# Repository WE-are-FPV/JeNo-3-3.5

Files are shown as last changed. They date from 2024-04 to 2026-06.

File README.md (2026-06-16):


> [!NOTE]
> Current version : **1.2.1** (read [changelog](#changelog) for details)

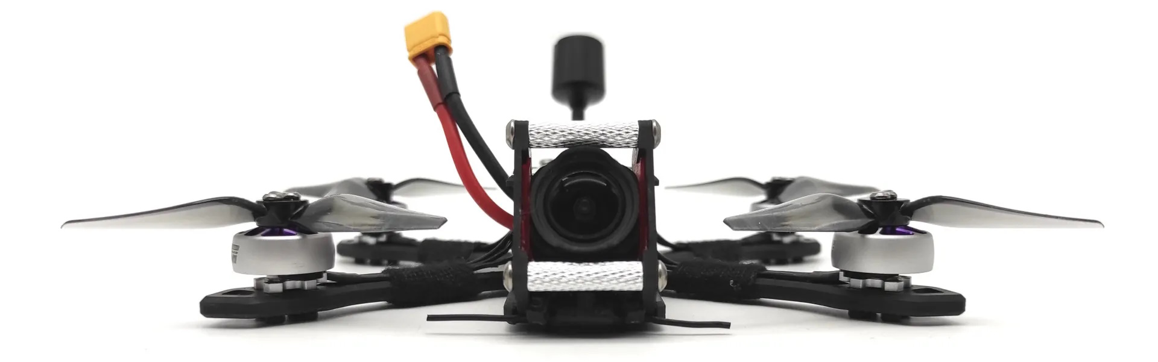
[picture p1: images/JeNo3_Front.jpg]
JeNo 3 - Front view


# JeNo 3" and 3.5"
***3-3.5" drone FPV frame compatible with Air Unit O3 and O4 Pro, designed for Freestyle, Freeride and Cinematic. Many customizable options are available.***

> [!NOTE]
> Designed in France by members of the [WE are FPV](https://www.wearefpv.fr/) community, the JeNo is already flown by hundreds of pilots and is now being sold by [Drone FPV Racer](https://www.drone-fpv-racer.com/jeno-3-frame-kit-we-are-fpv-12958.html?aff=64&id_campaign=13) (affiliate link). The French version of the project is available on [Printables](https://www.printables.com/fr/model/459702-jeno-335-drone-frame). Note that a [2.5" version](https://github.com/WE-are-FPV/JeNo-Pocket), a [5.1-6" version](https://github.com/WE-are-FPV/JeNo-5.1) and a [7-8" version](https://github.com/WE-are-FPV/JeNo-7) of the JeNo exist.

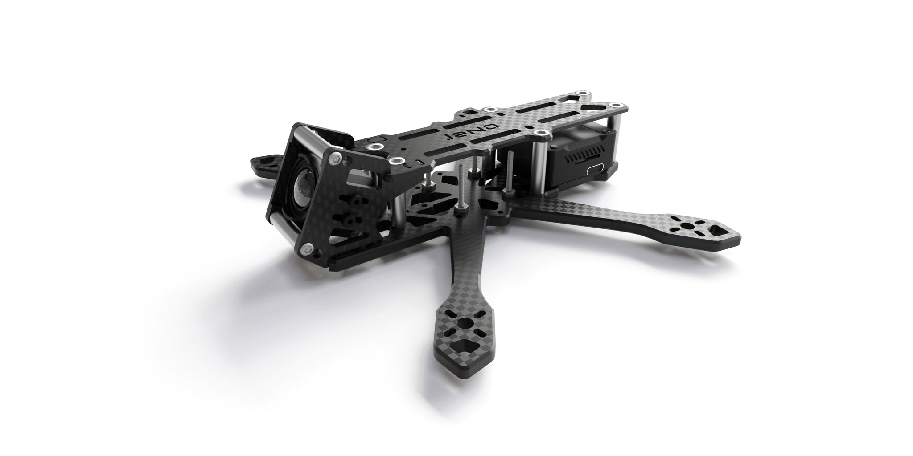
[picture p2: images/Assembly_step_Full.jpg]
JeNo classic - 3D render


## Table of contents

* [Key features](#key-features)
* [Presentation](#presentation)
* [Detailed specifications](#detailed-specifications)
* [Versions and files](#versions-and-files)
* [Customization](#customization)
* [Buy it or cut it !](#buy-it-or-cut-it-)
* [Bill of materials](#bill-of-materials)
* [Building/Assembly guide](#buildingassembly-guide)
* [Inspiration](#inspiration)
* [Tuning, Betaflight Preset ?](#tuning-betaflight-preset-)
* [Blackbox](#blackbox)
* [Videos](#videos)
* [Builds examples](#builds-examples)
* [Authors](#authors)
* [TPU](#tpu)
* [Community (remixes and TPU)](#community-remixes-and-tpu)
* [Changelog](#changelog)

## Key features
- [x] **Sturdiness** and **rigidity**
- [x] Excellent flight **performances**, easy to tune
- [x] **Wide-X** geometry
- [x] Perfect DJI **Air Unit O3 or O4 Pro** camera integration
- [x] Optional soft mounting of the camera for effective Gyroflow stabilization.
- [x] Designed for : DJI Vista/AU O3/AU O4 Pro, WalkSnail, HDZero, Analogic
- [x] **Frame and standoffs NOT visible** in video feed, with any FPV camera
- [x] **Props NOT visible** in video feed !
- [x] Support 20x20 stacks as well as AiO (straight and 45° angled)
- [x] **Customizable** (weight, size, camera plates, unibody or not)

## Presentation
The success of the [JeNo 5.1"](https://github.com/WE-are-FPV/JeNo-5.1) has led us to develop a little brother, in **3 and 3.5"** form factor. This frame will therefore be just **as comfortable for Freestyle as for cinematic** shooting.

On 5" and larger builds, we might be tempted to keep an Action Cam, whereas on a **compact and light machine**, the **DJI O3/O4 Pro reveals its full potential**.

The design of a frame of this size turned out to be more delicate than expected :

* **Weight** is crucial
* **Strength** and **rigidity** remain major concerns
* **Electronics** are more **diversified** : 20x20 stack with separate FC and ESCs, AiO straight or angled at 45°, stack mounting with M2 or M3...
* The low inertia of this format makes the gyro of the O3/O4 Pro camera very sensitive; vibration tolerance is much lower than for a 5" quads
* **Clear FOV** : no spacers, frame, or visible propellers in the FPV feed

After several iterations, we have come to a first version of the JeNo that **ticks all these boxes !** This is the **3" Classic version, unibody with a 4mm bottom plate**.

We were initially not enthusiastic about the unibody design, but this approach has proven to be an **excellent compromise**. With a thickness of 4mm for the bottom plate, we get **exceptional strength** and **flight behavior** worthy of a 5". The assembly remains easy, and the absence of separate arms allows for sliding a 20x20 stack while taking advantage of the 20mm height of the body.

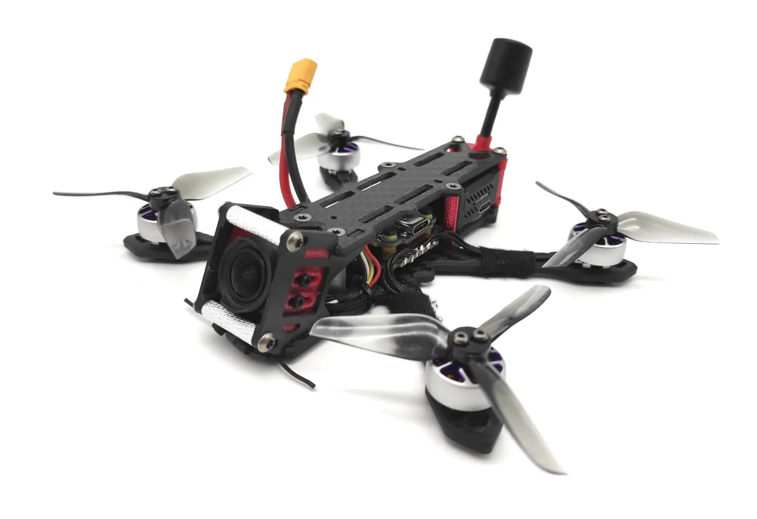
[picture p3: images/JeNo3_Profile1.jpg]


**Other versions** are available :

* 3.5" (unibody) (warning : tips of props slightly visible in the FPV feed)
* 3" (unibody) **Light**
* 3" et 3.5 " with **separate arms**
* 4": this is a variation created by Kennytak, and the necessary files are available on [his page](https://www.printables.com/fr/model/516544-jeno-4-unibody-drone-frame-for-dji03-airunit-vista). The props remain slightly visible in the FPV feed.

The **JeNo 3** follows in the footsteps of its big brother : the front cage tilted at 25° provides a **clear FOV**. Notches are provided to slide in any type of **ND filter**, and the propellers are not visible in the FPV feed or in HD recording.

Be cautious, though—when using an O4 Pro, make sure to get vertical ND filters, like [those from GEPRC](https://geprc.com/product/geprc-dji-o4-air-unit-pro-filter/).

Two types of camera plates are available : **full carbon** or **soft-mounted**. Note that to benefit from Gyroflow (or RockSteady) stabilization, it is **imperative to opt for the soft-mounted camera plates**.

Finally, as this frame was designed by members of the [WE are FPV](https://www.wearefpv.fr/) **community**, a **"WaF edition"** is available (the logo is engraved on the bottom plate). Join us on the WAF forum in [the official JeNo 3-3.5" thread](https://forum.wearefpv.fr/topic/20437-jeno-335-un-ch%C3%A2ssis-compact-taill%C3%A9-pour-le-dji-o3/) to discuss it further.

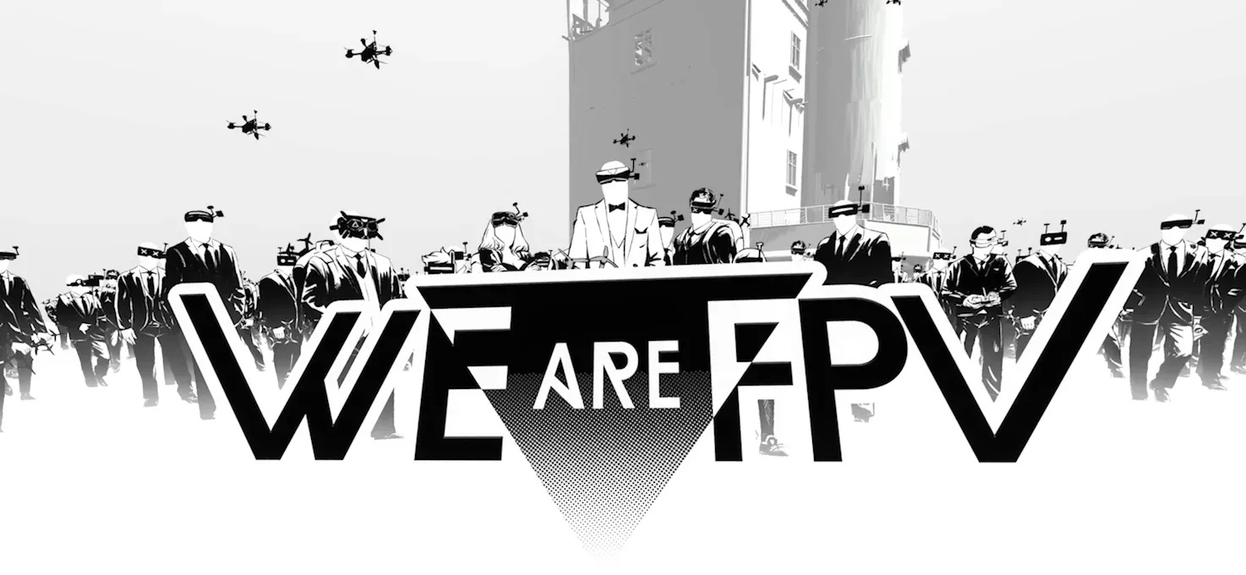
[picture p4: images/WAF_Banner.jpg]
WE are FPV banner


The JeNo is also available in [2.5" version](https://github.com/WE-are-FPV/JeNo-Pocket), [5.1" and 6" version](https://github.com/WE-are-FPV/JeNo-5.1) and [7" and 8" version](https://github.com/WE-are-FPV/JeNo-7).

## Detailed specifications

||| 
| :--- | :--- |
| **Geometry** | **Wide-X** | 
| **Props size** | 3 to 3.5" (depending on the versions) | 
| **Weight** | **40 to 55 g** depending on the versions, including screws | 
| **Arms** | **4mm** for unibody, **3mm** for separate arms | 
| **Body height** | 20 mm | 
| **Stack height** | 20 mm (unibody) | 
| **Bottom plate** | **4mm** for unibody, **2mm** for separate arms | 
| **Middle plate** | 2 mm (separate arms) | 
| **Top plate** | 2 mm | 
| **Camera plates** | 2.5 mm | 
| **Motors mounting** | 9 to 12 mm | 
| **Camera** | 20 mm (DJI), Micro, Nano. **Clear FOV**. Ajustable.
| **Main stack** | 25.5 mm x 25.5 mm (M2) AiO and 20 mm x 20 mm (M2) stack | 
| **Supported VTX** | Analogic, DJI Vista, **DJI Air Unit O3/O4 Pro**, WalkSnail, HDZero… | 
| **Strap passage** | Yes | 

## Versions and files

### Versioning
You will find the **current version** of the frame at the beginning of the description and the full [history of modifications](#changelog) at the end of the page.

We strongly recommend always cutting the latest version to ensure you benefit from the most recent optimizations.

The version **number format** is as follows :
```
<Major versions>.<Minor version>.<Revision>
ex : 1.3.2
```

* **Revision :** This number is incremented in the case of minor modifications with no significant impact.
* **Minor version :** This number is incremented for minor modifications that may potentially break compatibility with certain TPU parts.
* **Major version :** This number is incremented for significant modifications that break compatibility at the carbon level.

Since the creation of the JeNo 3", we have always strived to **maintain compatibility at the carbon level**. As a result, the version remains “1.x.y.”

In practical terms, this means that if you have the very first version of the JeNo 3" and want to equip it with the **O4 Pro**, you only need to have new camera plates cut—they will be compatible with your frame version!

**Note :** If you develop TPU parts for the JeNo, be sure to specify the version they are compatible with.

### Files management
To simplify things, we have reorganized the file structure. The files are now divided into **five groups** :

* **01-FRAME :** Contains **models** describing the **frame** in DXF, STEP, and STL formats for the current version. Also contains a PDF file which is a reformatted version of the DXF.
* **02-TPU :** Contains **TPU models** for the current frame version in STL format.
* **03-FRAME-HISTORY :** Contains previous versions of the frame.
* **04-TPU-HISTORY :** Contains TPU models that are no longer compatible with the current version.
* **OTHER-FILES :** Contains documentation files, including the assembly manual and a description.

The major change is that all options are now consolidated into a single file. This will make version management significantly easier for us.

If you want to view the DXF file with all annotations, we recommend using the free software [DWG TrueView](https://www.autodesk.com/products/dwg-trueview/overview). If you prefer not to use it, the PDF version of the file will contain all the necessary information.

## Customization

The JeNo is customizable, offering several **options** to best adapt to different needs and individual preferences : 

* **3" Unibody 4mm Classic :** This is the first version made available. Designed for **freestyle** due to its strength, it will also be suitable for **cinematic** use with soft-mounted camera plates. 100% clear FOV. This version uses **M3** screws and standoffs.
* **3" Unibody 4mm Light :** Sacrificing some strength and rigidity for more lightweight, thus increasing autonomy, and switching to **M2** screws/spacers. A chassis more oriented towards cinematic use. Note that M2 standoffs are more difficult to source.
* **3.5" Unibody 4mm :** For those seeking a bit more **inertia and stability**, or possibly for mid-range use. _**Note: the propellers are very slightly visible in the FPV feed. With black propellers, they will be practically invisible.**_
* **Separate arms :** For those wary of unibody designs ;) a 3" version and a 3.5" version (only the length of the arms changes). _**Note: AIO strongly recommended; stacks will struggle to fit due to the low remaining height in the body = low profile !**_

Several versions of 25° camera plates are available :

* **Freestyle** (full carbon): Optimized for the O3.
* **Cinematic** (soft-mounted): Optimized for the O3.
* **M2 versions** for the Light edition.
* **Freestyle O4 Pro** (full carbon): Optimized for the O4 and compatible with the O3.
* **Cinematic O4 Pro** (soft-mounted): Optimized for the O4 and compatible with the O3.

A [high tilt version](https://www.thingiverse.com/thing:6584519) (40°) is available in community remixes (by [Bard Fpv](https://www.youtube.com/@bardfpv)) for the O3.

> [!IMPORTANT]
> Please note that to benefit from Gyroflow (or RockSteady) stabilization, **soft mounting is mandatory**.

> [!IMPORTANT]
By default, we have left the stack holes at a 2mm diameter (M2). If your stack uses M3 screws, you will need to enlarge these holes. Please note, carbon dust is hazardous, to avoid inhaling it, run a trickle of water while drilling/filing.

For your information, we have tested this frame with the following setup:

* **Recommended Motors :** 1404, 4000 to 4500KV for 3"
* **Recommended Batteries :** 4S / 550mAh for Freestyle, up to 850mAh for cinematic cruising
* **Recommended Props :** T3x2.5x3 & HQ T3x3x3

Below, you will find a complete build example as well as several flight videos with this setup.

## Buy it or cut it !

It is up to you : you can get it cut or you can get it from a shop. If you're not looking for a specific option, note that Drone FPV Racer offers the JeNo 3" in the classic version, along with all spare parts, prints, and lipo pads. La Camera Embarquée also offers the JeNo 3 and 3.5".

* [JeNo 3" by DFR](https://www.drone-fpv-racer.com/jeno-3-frame-kit-we-are-fpv-12958.html?aff=64&id_campaign=13) (affiliate link)
* [JeNo 3" by DFR](https://www.lacameraembarquee.fr/we-are-fpv/17773-chassis-we-are-fpv-jeno-3.html)
* [JeNo 3.5" by DFR](https://www.lacameraembarquee.fr/we-are-fpv/17776-chassis-we-are-fpv-jeno-35.html)
* [FPV CNC Drone](https://fpvcncdrone.com/)

The JeNo 3" and all its variations are also available from [CNC Madness](https://cncdrones.com/WE-are-FPV_c_118.html) (Canada).

Of course, you can directly contact your favourite carbon fiber cutting service.

Note: Prices are often excellent in stores, but they don’t always offer the latest version.

The ["01-FRAME"](https://github.com/WE-are-FPV/JeNo-3-3.5/tree/main/01-FRAME) folder contains all the files you need to get it **cut** in your favourite flavour.

Consult the **DXF file** of the frame (or the PDF version) to choose the version that interests you.

Feel free to select a pre-made "Edition" (Classic, Light, or Bando), or mix different options and choose certain "extras".

You will also need to choose a type of camera plates (classic, cine, etc.).

> [!NOTE]
> All parts versions are compatible with each others

## Bill of materials

In addition to the carbon fiber, you will need the following hardware to complete the assembly of the frame.

**Standoffs**

It is recommended to use 5mm diameter standoffs, especially for those that will serve as support for TPU (backpack and capacitor). Moletted standoffs can still be used, but the TPU supports will need to be modified accordingly.

> [!WARNING]
> Attention: For the Light version, you will need to provide M2 standoffs and corresponding screws (M2 instead of M3)

| Quantity | Description | Details |
| :---: | :--- | :--- |
| 6 | M3x20mm standoffs | for the body |
| 2 | M3x20mm standoffs | for the camera |

**Stack materials**

> [!WARNING]
> Attention: M2 screws are mentioned here because they are most commonly found in this format. However, some 20x20 stacks use M3 screws. In this case, you will need to enlarge the stack holes.

* If 25.5x25.5 AiO

| Quantity | Description | Details |
| :---: | :--- | :--- |
| 4 | M2x16mm | for the stack |
| 4 | M2 nuts for stack screws | |

* If 20x20 stack

| Quantity | Description | Details |
| :---: | :--- | :--- |
| 4 | M2x20mm countersunk screws | for the stack |
| 4 | M2 nuts for stack screws | |

**Frame materials**

| Quantity | Description | Details |
| :---: | :--- | :--- |
| 6 | M3x6/8mm countersunk screws | for the top plate |
| 10 | M3x8mm screws (titanium if possible) | for the bottom and camera plates |

**Additional materials**

| Quantity | Description | Details |
| :---: | :--- | :--- |
| 16 | M2x7mm screws (if using arms protections) or M2x6mm (if no TPU) | for the motors |
| 4 | M2x3mm screws if soft mounted or M2x4mm if NOT softmounted | for the camera |

**Additional materials for separate arms versions**

| Quantity | Description | Details |
| :---: | :--- | :--- |
| 5 | Pressnuts ([Flywoo](https://www.drone-fpv-racer.com/flywoo-m3-clinch-nuts-20-pcs-7965.html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) or SourceOne alike) | 4 for the arms, 1 for the middle plate |
| 5 | M3x10mm screws | for the pressnuts |

**Fasten the lipos**

The JeNo allows the use of non-slip straps thanks to its strap slots. You can also use a LiPo pad if desired.

## Building/Assembly guide

Find numerous examples of builds on the _**DroneBuilds**_ page of WE are FPV.
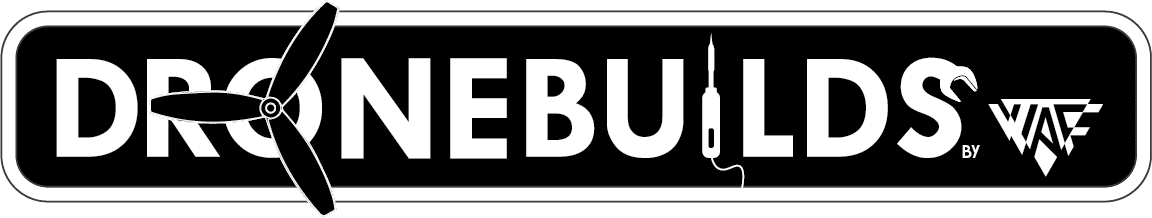
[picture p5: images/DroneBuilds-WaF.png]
DroneBuilds (https://forum.wearefpv.fr/71-dronebuilds/ "DroneBuilds - Click to Access!")


Some **clarifications** before assembling the frame:

* If your electronics require M3 screws, you will need to slightly enlarge the holes, originally designed for M2 (taking care not to inhale carbon dust)
* You can use the front standoffs to attach a capacitor and/or an RX :

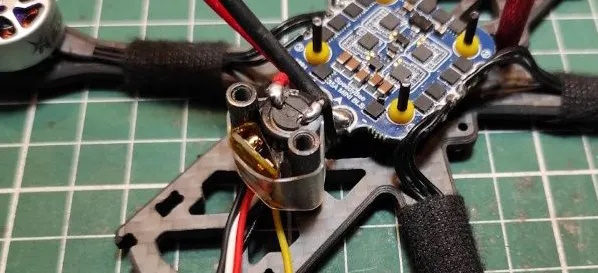
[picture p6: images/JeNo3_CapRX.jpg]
JeNo 3 Capacitor and RX


* The RX antenna can be attached to the front of the quad using zip ties (TPU front bumper also allow to fix the RX antenna)

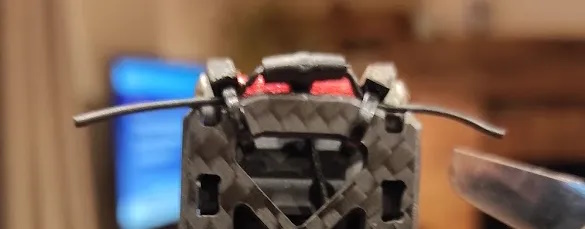
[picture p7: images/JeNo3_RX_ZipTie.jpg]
JeNo 3 RX Antenna


The assembly is simple (you can also find the detailed [assembly instructions in PDF format](https://github.com/WE-are-FPV/JeNo-3-3.5/blob/main/OTHER-FILES/JeNo3_Assembly_Guide_EN.pdf) among the project files) :

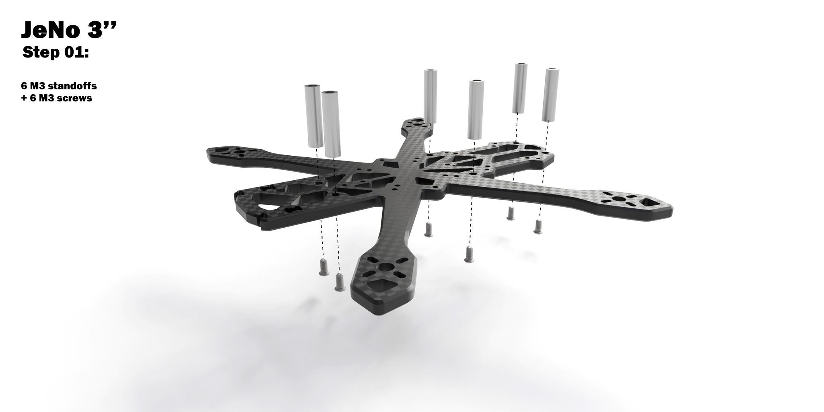
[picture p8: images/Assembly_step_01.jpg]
JeNo 3 Assembly step 01


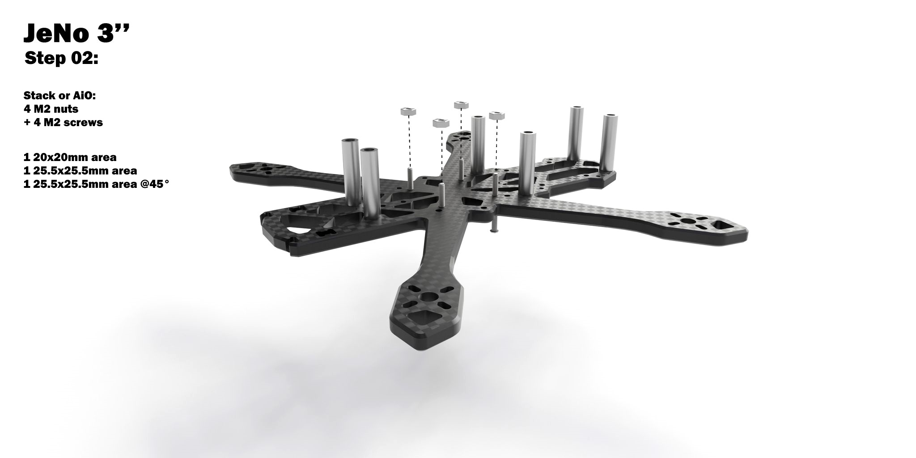
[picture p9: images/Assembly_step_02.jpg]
JeNo 3 Assembly step 02


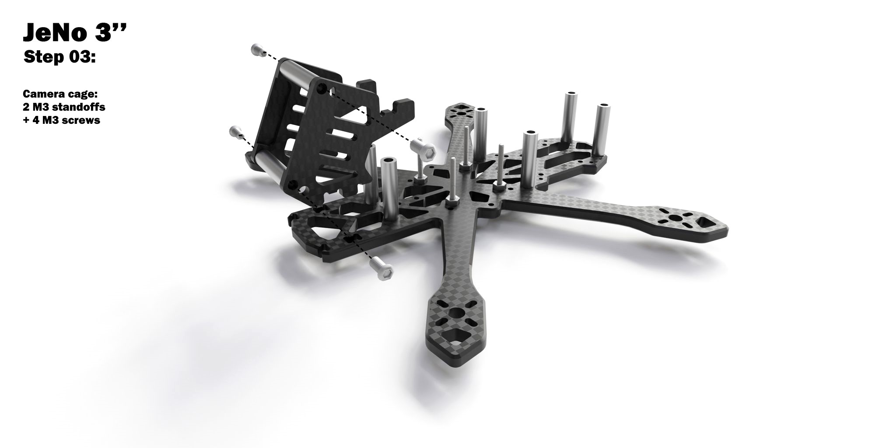
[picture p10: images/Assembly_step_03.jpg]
JeNo 3 Assembly step 03


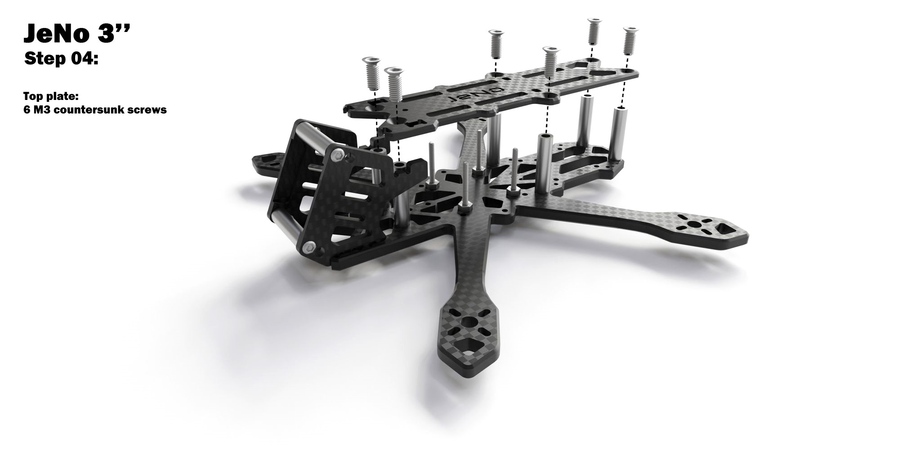
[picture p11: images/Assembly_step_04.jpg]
JeNo 3 Assembly step 04


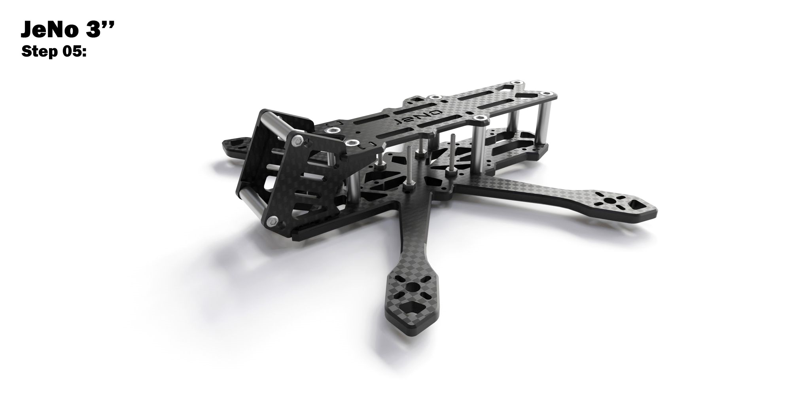
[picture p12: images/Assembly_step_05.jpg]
JeNo 3 Assembly step 05


## Inspiration
It is primarily inspired by its big brother, the [JeNo 5.1"](https://github.com/WE-are-FPV/JeNo-5.1), especially for the camera plates system.

## Tuning, Betaflight Preset ?
For the JeNo 5.1", we provided a preset.

For the 3", we will not share a preset in the short term because there are **too many factors** that can alter the quad's behavior:

* Bottom plate thickness
* Stack VS AiO (the latter often being much noisier)
* M3 screws and spacers vs M2
* 3" props vs 3.5"
* Capacitor or not
* etc.

If, with a little more perspective, we see that a preset is feasible, we will share it. In the meantime, we have shared some settings that should work with most setups in [this post](https://forum.wearefpv.fr/topic/20437-jeno-335-un-ch%C3%A2ssis-compact-taill%C3%A9-pour-le-dji-o3/page/10/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).

However, one piece of advice, if you find your quad too challenging to handle in confined spaces, do not hesitate to adjust the throttle curve by adding a bit of expo around the "hover point" :

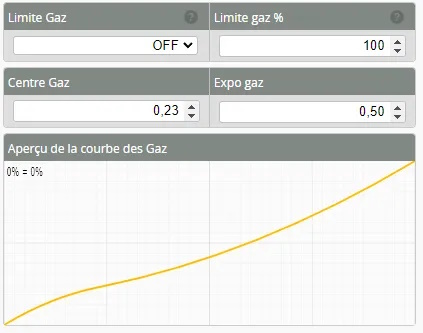
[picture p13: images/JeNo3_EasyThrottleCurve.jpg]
JeNo 3 Throttle curve


## Blackbox
Here is an overview of vibration distribution on the 3 axes for the JeNo 3" 4mm Unibody. This is indeed the **unfiltered** gyro signal freestyle flight :

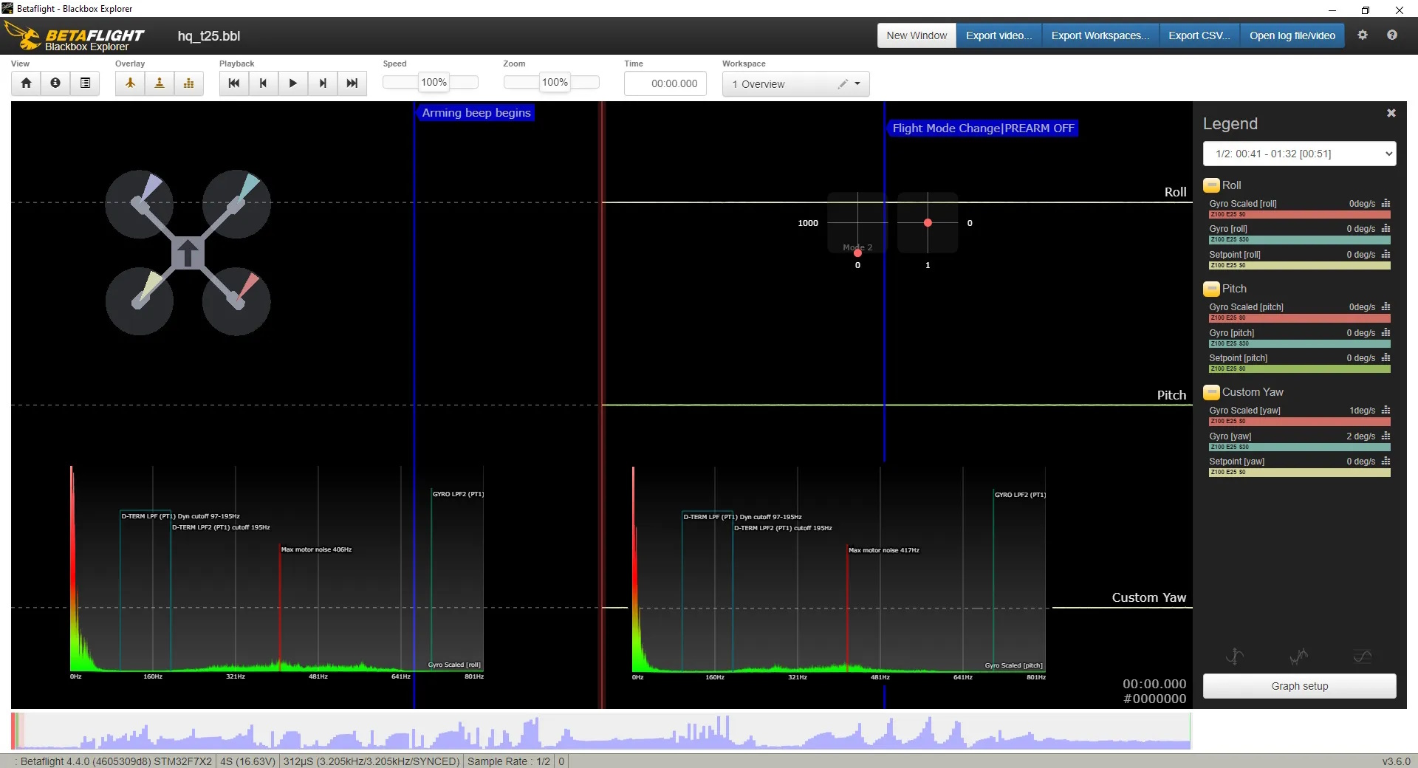
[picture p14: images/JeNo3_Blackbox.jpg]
JeNo 3 Blackbox


## Videos
Flight preview of the JeNo 3" Unibody Classic 4mm version (Cinematic, camera plates soft-mounted), stabilized with Gyroflow :

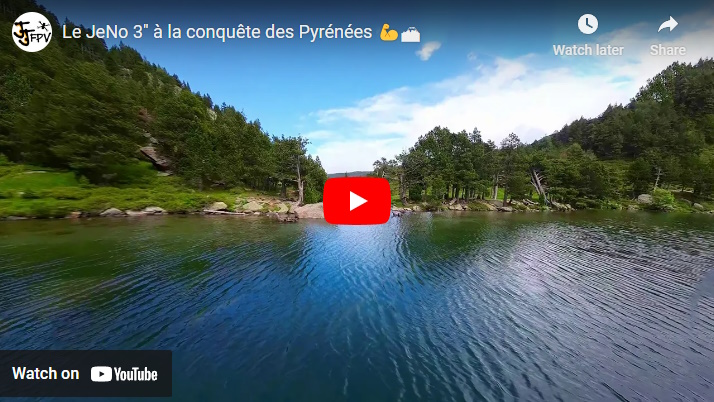
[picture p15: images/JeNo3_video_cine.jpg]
JeNo 3" Cinematic (https://www.youtube.com/watch?v=Bba9C5jj3qI "JeNo 3 Cinematic - Click to Watch!")


Flight preview of the JeNo 3" Unibody Classic 4mm version (Freestyle) :

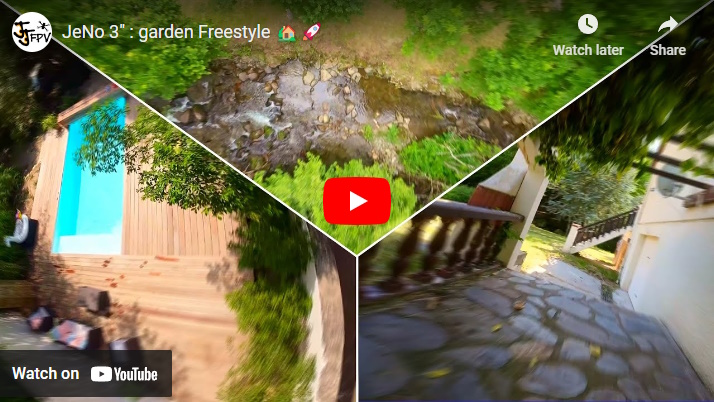
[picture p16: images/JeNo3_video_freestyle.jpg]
JeNo 3" Freestyle (https://www.youtube.com/watch?v=a-RcqAQSSa8 "JeNo 3 Freestyle - Click to Watch!")


Flight preview of the JeNo 3" Unibody Classic 4mm version (Bando):

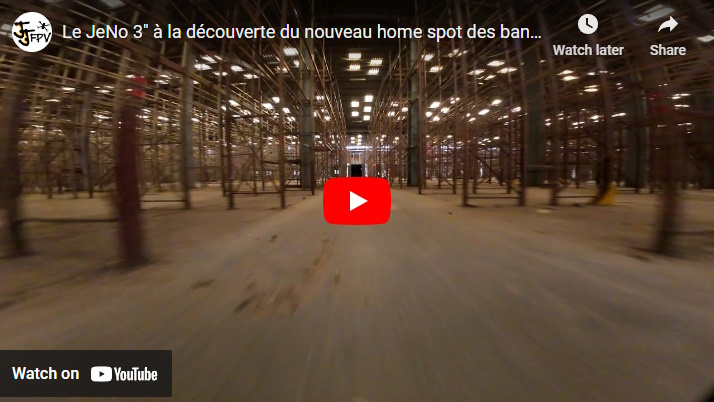
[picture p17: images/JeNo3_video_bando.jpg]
JeNo 3" Bando (https://www.youtube.com/watch?v=Iw_Cw9_1gNU "JeNo 3 Bando - Click to Watch!")


JeNo 3" review on WE are FPV (French) :

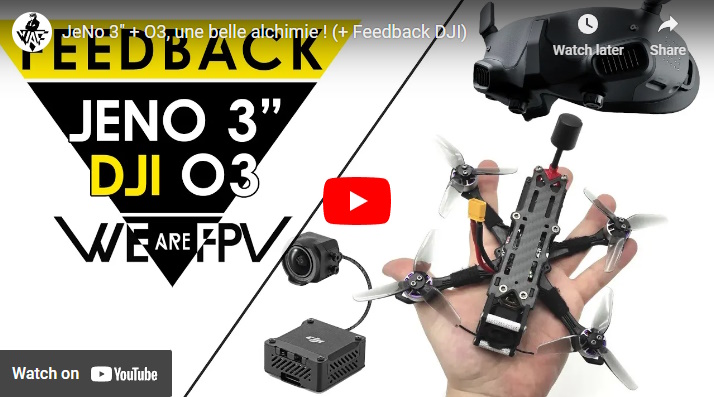
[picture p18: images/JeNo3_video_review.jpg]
JeNo 3" Review (https://www.youtube.com/watch?v=-c4rGYWvYhU "JeNo 3 Review - Click to Watch!")


## Builds examples

You can find many build examples on [WE are FPV's DroneBuilds](https://forum.wearefpv.fr/71-dronebuilds/) :

* fr : [JeNo 3 Prototype](https://forum.wearefpv.fr/topic/20327-proto-jeno-3/) (this one)
* fr : [JeNo 3" AiO AT32/AM32](https://forum.wearefpv.fr/topic/21637-jeno-3-aio-at32am32/)
* fr : [JeNo 3.5" O3](https://forum.wearefpv.fr/topic/20480-jeno-35_o3/)
* fr : [JeNo 3" (6s)](https://forum.wearefpv.fr/topic/22032-jeno-3-mais-en-6s-et-sous-testost%C3%A9rone/)
* fr : [Jeno 3" (Kiss)](https://forum.wearefpv.fr/topic/21647-jeno-3-kiss/)
* fr : [jeno3 light](https://forum.wearefpv.fr/topic/22677-jeno3-light/)
* ...

## Authors

The JeNo was designed by :

* nochamo - [Youtube](https://www.youtube.com/user/nochamo)
* Jerome / Jéjé FPV - [Youtube](https://www.youtube.com/@jejefpv)

## TPU
Among the [downloadable files](https://github.com/WE-are-FPV/JeNo-3-3.5/tree/main/tpu), you will find a variety of TPU to protect your JeNo 3" :

* **VTX Antenna** mounts
* Front and back **bumpers**
* **Nano camera** adapter
* Camera **softmount**
* Several arms **protections**

## Community (remixes and TPU)

**Fork/remix**

* [JeNo 4"](https://www.printables.com/fr/model/516544-jeno-4-freestyleracing-drone-frame-for-dji03-airun) by [Kennytak](https://www.printables.com/fr/@Kennytak_77000)

**TPU**

In addition to the TPU options available on [this repo](https://github.com/WE-are-FPV/JeNo-3-3.5/tree/main/tpu), you will find here some TPU designs created by the community.

* [TPU set for JeNo 3.5"](https://www.printables.com/fr/model/533320-tpu-pour-jeno-35) by Xavier Robin
* [GPS and O3 antenna mounts](https://www.printables.com/fr/model/595138-jeno-3-antenne-option-gps-18x18x8) by Olivier
* [Shark fin to protect the lipo](https://www.thingiverse.com/thing:6416888) by vfr150878
* [Backpack O3 antenna + GPS M10 mini](https://www.printables.com/fr/model/794568-jeno-3) by [Cirbaf](https://www.printables.com/fr/@Cirbaf_1779503)
* [Arms/motors bando protections](https://www.printables.com/fr/model/649175-bando-boots-jeno-3p) by Julien
* [Runcam Thumb mount](https://www.printables.com/fr/model/647336-mount-runcam-thumb-pour-jeno3)by [Tamm'c](https://www.printables.com/fr/@TammC_1383304)
* [TPU set + 40° high tilt camera plates](https://www.thingiverse.com/thing:6584519) by [Bard Fpv](https://www.youtube.com/@bardfpv)
* [Front bumper](https://www.printables.com/fr/model/876097-bumper-jeno-3) by [Nox](https://www.printables.com/fr/@NOX_1685274)
* [M10 Mini Support, Cap, ViFly Finder, O3 Antenna](https://www.printables.com/fr/@NnJj_1076330/models) by [Nn Jj](https://www.printables.com/fr/@NnJj_1076330)
* [Full TPU set, compatible with COB LEDs](https://makerworld.com/en/models/551883) by [BinaryWhite](https://www.youtube.com/@focal3drone803)
* [Propguards to turn the JeNo 3 into a Cinewhoop](https://www.printables.com/fr/model/991129-jeno-3-cinewhoop-cage) by [Nn Jj](https://www.printables.com/fr/@NnJj_1076330)
* [TPU set](https://www.printables.com/fr/model/894556-jeno-3-tpu-pack) by [Nono31](https://www.printables.com/fr/@Nono31_454985)
* [Mount for buzzer/LED HGLRC](https://www.printables.com/fr/model/964655-jeno_3inch_antenne-hglrc-ws2812b-beeperled) by [Bruce Vanderro / Rawaï](https://www.printables.com/fr/@BruceVanderr_2315800)
* [Backpack O3 / ViFly Finder Mini](https://www.printables.com/fr/model/991436-jeno-3-support-antenne-03-buzzer-vifly-finder-mini) by [jrvaille](https://www.printables.com/fr/@jrvaille_2317118)

## Changelog

> [!TIP]
> Compatibility is consistently maintained between each version: if your frame was a v1, the parts from v1.2 will be compatible. The same applies to TPU accessories. That's why we don't keep the history of previous versions.

* 23/05/2025 :
  * Fix for softmounted O4 Pro camera plates and O4 Pro antennas
  * Addition of TPU for Flyfish GPS (for O4 Pro camera plates), front bumper (for O4 Pro camera plates), capacitor hat
* 16/02/2025 : 
  * Addition of TPU for softmounted camera plates (works with O3 and O4)
* Version **1.2.1** (01/02/2025) : 
  * Support for the **Air Unit O4 Pro** (camera plates + TPU)
  * The new O4 camera plates are also compatible with the O3
  * Les anciennes camera plates O3 restent plus petites
* Version **1.1.0** :
  * Removal of the holes on the arms, before the motors
* Version **1.0** (28/04/2023) :
  * Creation of this page
  * Sharing of the 3" Unibody 4mm Classic version
  * Sharing of the 3.5" Unibody 4mm Classic version

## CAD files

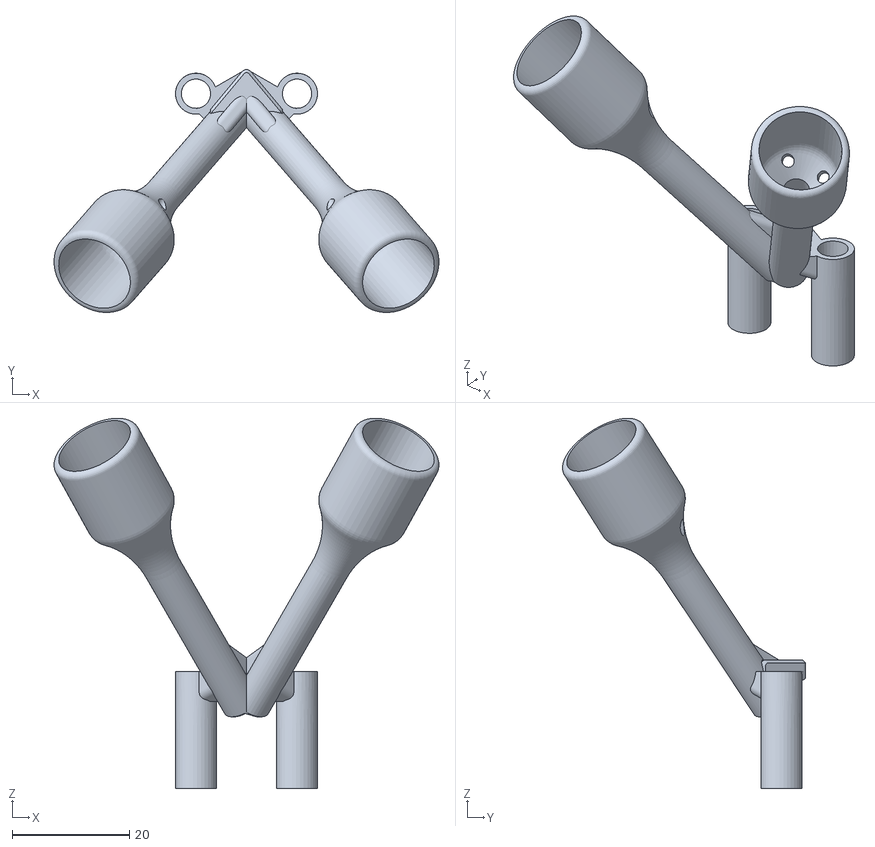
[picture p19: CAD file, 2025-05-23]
02-TPU/JeNo3_Antenna_O4_Pro_Full.stl
65.7 x 41.5 x 63.2

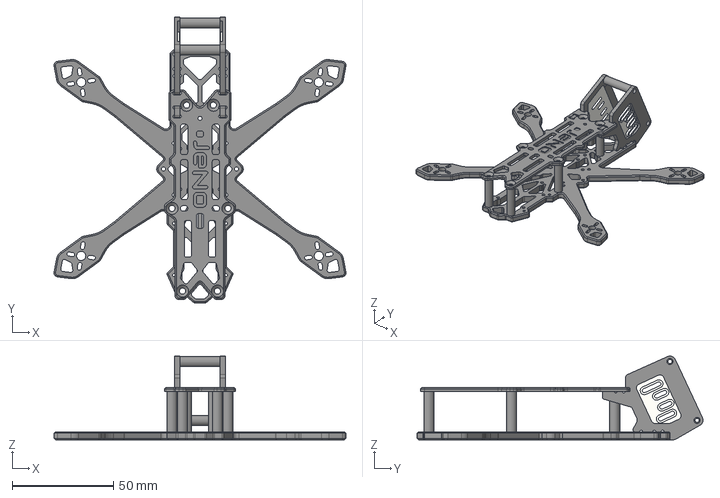
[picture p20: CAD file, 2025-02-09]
01-FRAME/JeNo3_ALL_VERSIONS_1.2.1.step
144.2 x 141.2 x 41.4 mm

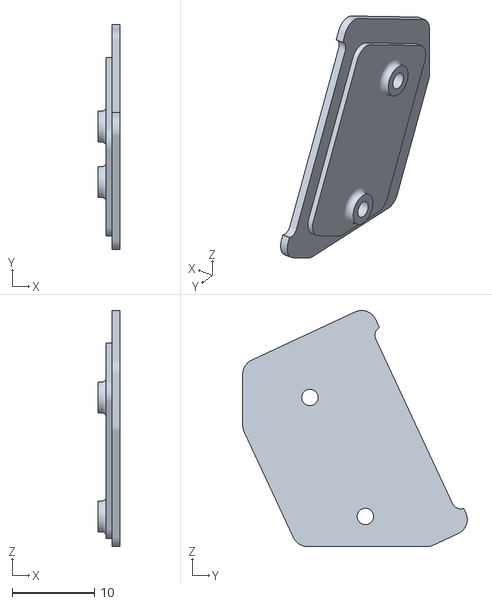
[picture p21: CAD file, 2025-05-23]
02-TPU/JeNo3_O4Pro_FixedCamPlate_Left.stl
2.70 x 27.4 x 28.8

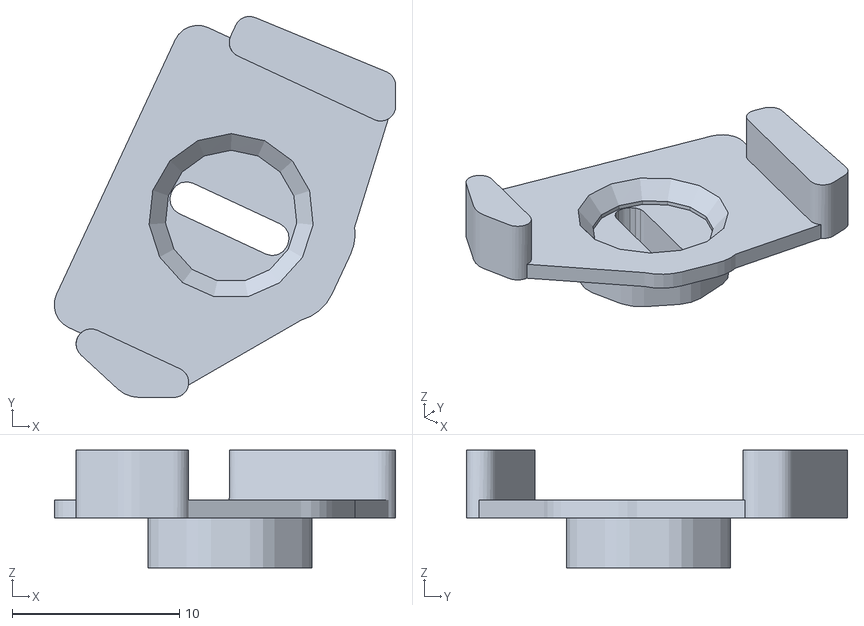
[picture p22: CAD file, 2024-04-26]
04-TPU-HISTORY/JeNo3_1.1_NanoCamera.stl
20.4 x 22.8 x 7.05

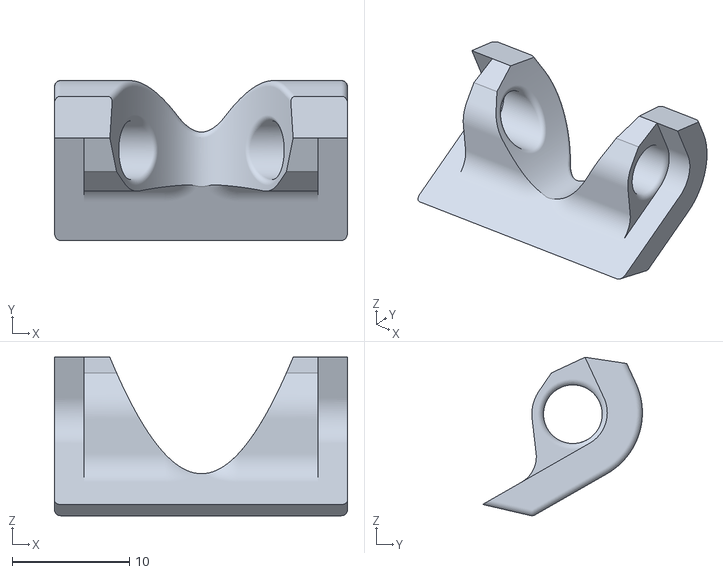
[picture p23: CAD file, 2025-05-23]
02-TPU/JeNo3_FrontBumper_O4_Pro.stl
25.0 x 13.6 x 13.5

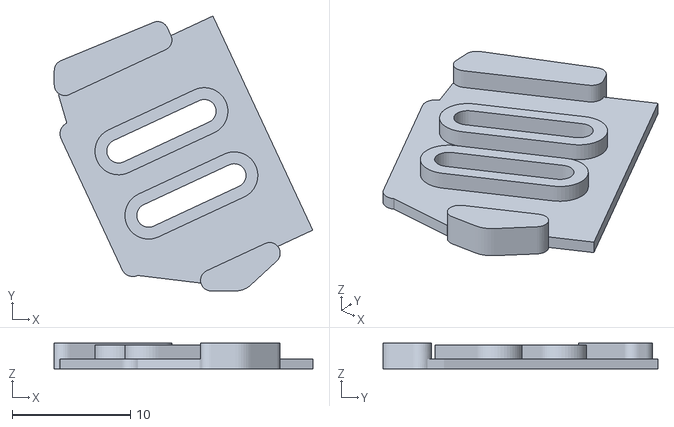
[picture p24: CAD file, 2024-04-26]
04-TPU-HISTORY/JeNo3_1.1_SoftMount_Right.stl
21.9 x 23.3 x 2.20

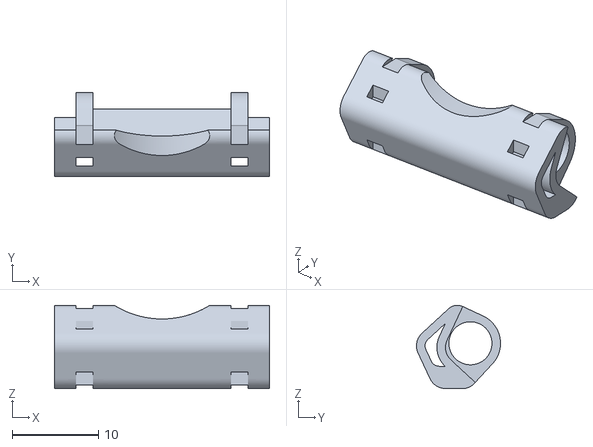
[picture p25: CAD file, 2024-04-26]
04-TPU-HISTORY/JeNo3_1.1_FrontBumper.stl
25.0 x 9.77 x 9.69

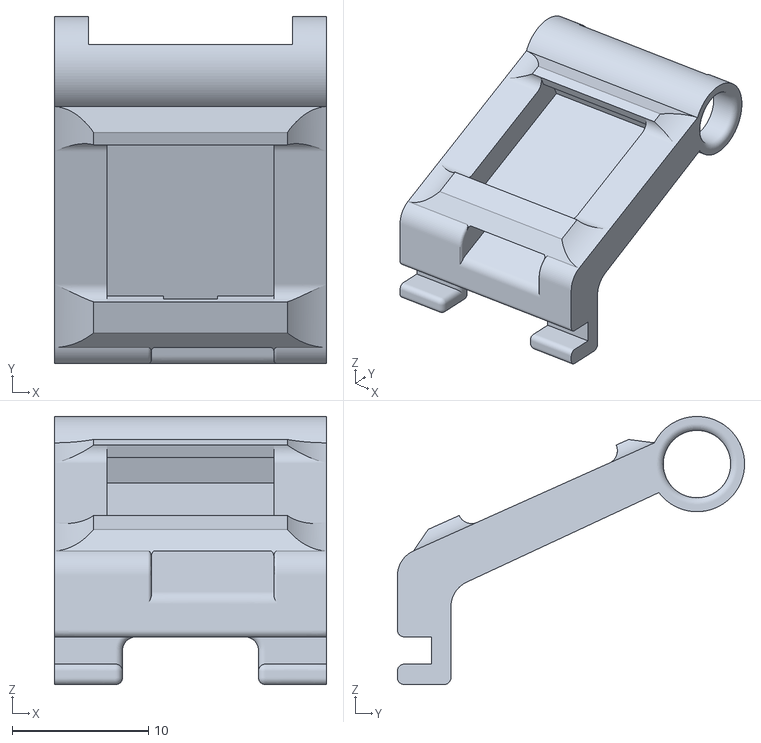
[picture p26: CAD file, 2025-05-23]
02-TPU/JeNo3_O4Pro_FlyFishGPS.stl
20.0 x 25.5 x 19.7

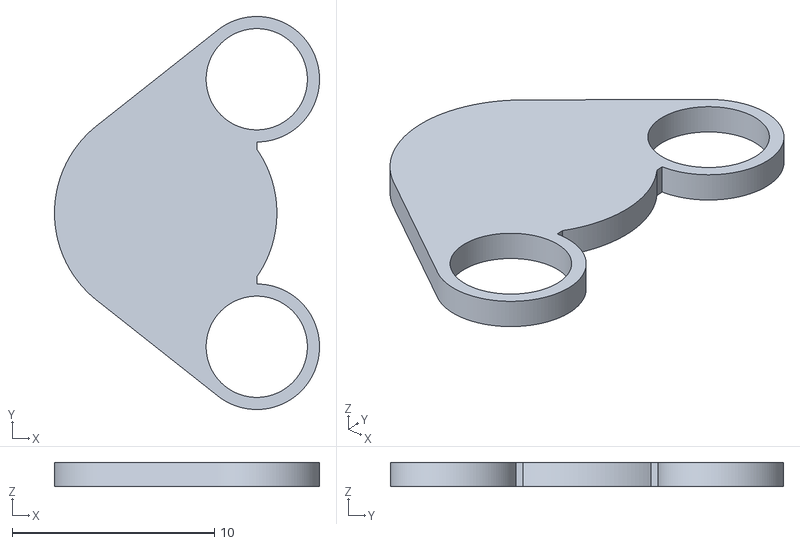
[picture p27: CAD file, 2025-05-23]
02-TPU/JeNo3_CapHat.stl
13.1 x 19.4 x 1.20

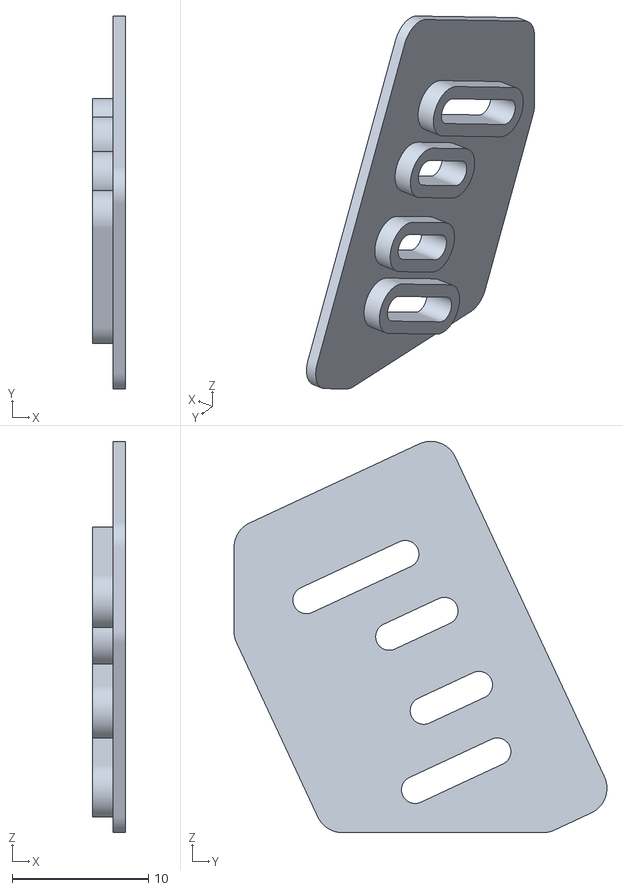
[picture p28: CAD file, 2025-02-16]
02-TPU/JeNo3_Softmount_O4_O3_Left.stl
2.40 x 27.4 x 28.7

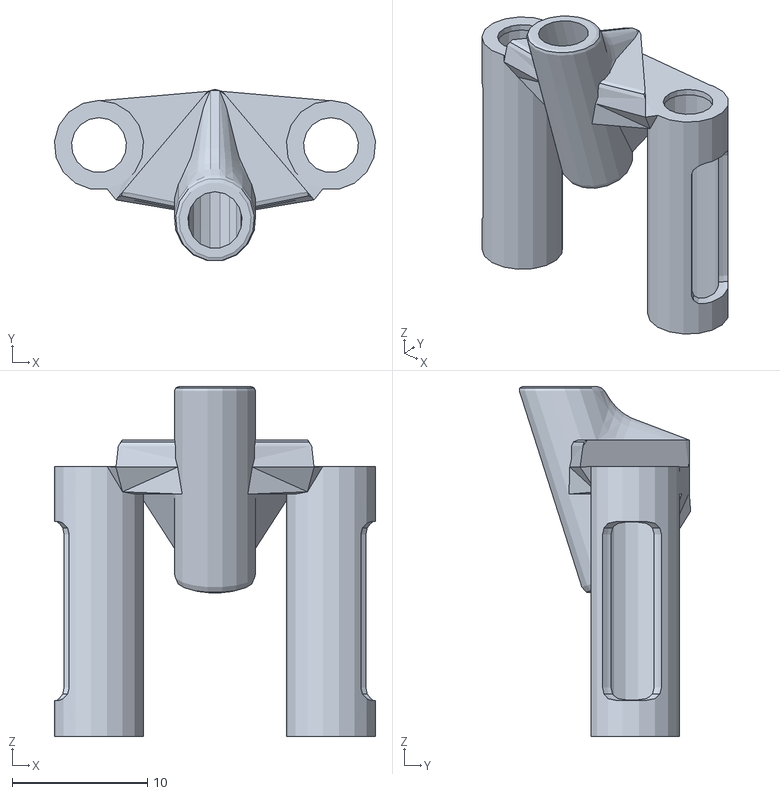
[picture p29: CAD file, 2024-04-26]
02-TPU/JeNo3_Antenna_VTX_M3.stl
23.8 x 12.7 x 25.9

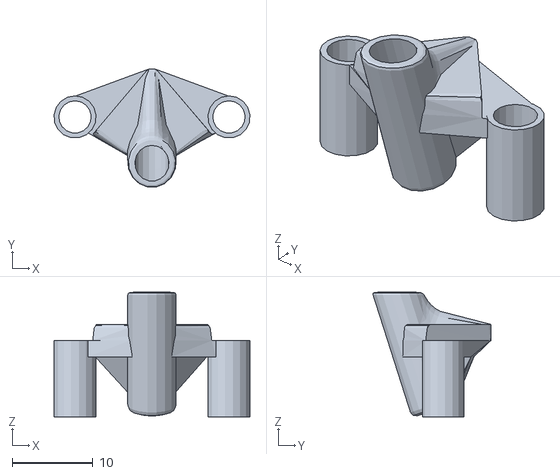
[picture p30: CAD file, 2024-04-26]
02-TPU/JeNo3_Antenna_VTX_M2.stl
24.2 x 14.6 x 15.4

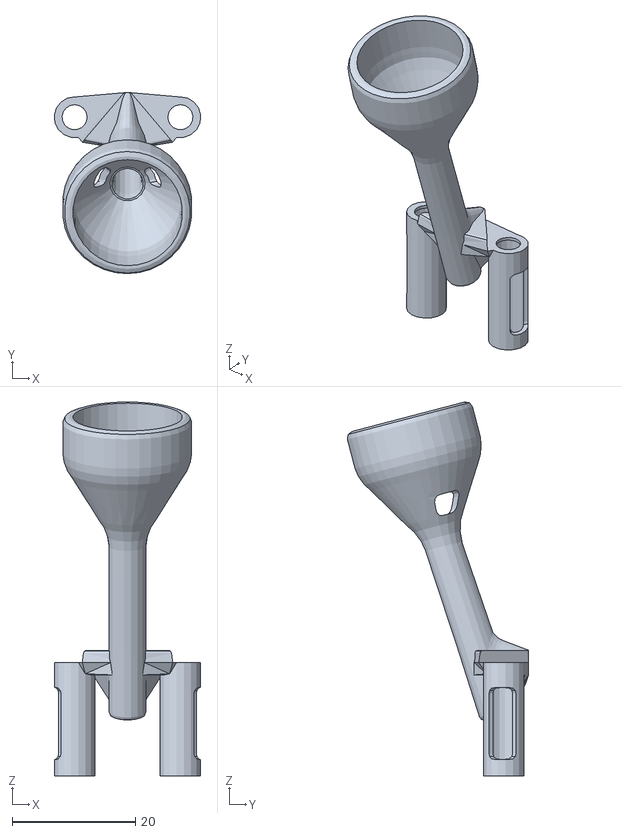
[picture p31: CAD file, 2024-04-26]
02-TPU/JeNo3_Bando_Antenna_O3.stl
23.8 x 29.4 x 60.7

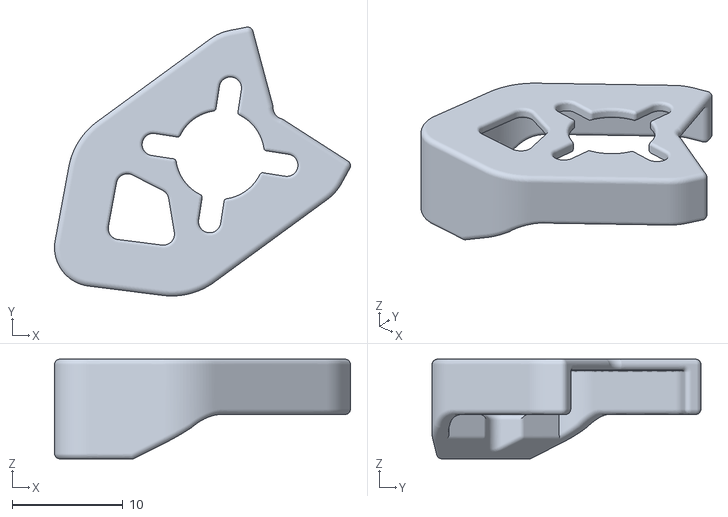
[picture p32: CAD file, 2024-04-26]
02-TPU/JeNo3_Arm_OpenLight.stl
26.7 x 24.3 x 9.00

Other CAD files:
03-FRAME-HISTORY/JeNo3_ALL_VERSIONS_1.1.dxf
02-TPU/JeNo3_O4Pro_FixedCamPlate_Right.stl
04-TPU-HISTORY/JeNo3_1.1_SoftMount_Left.stl
02-TPU/JeNo3_Softmount_O4_O3_Right.stl
01-FRAME/JeNo3_ALL_VERSIONS_1.2.1.dxf
01-FRAME/JeNo3_ALL_VERSIONS_1.2.1.stl
02-TPU/JeNo3_Arm_Light.stl
02-TPU/JeNo3_Arm_OpenUltraLight.stl
02-TPU/JeNo3_Arm_UltraLight.stl
02-TPU/JeNo3_BackBumper_Flat.stl
02-TPU/JeNo3_Bando_Arm.stl

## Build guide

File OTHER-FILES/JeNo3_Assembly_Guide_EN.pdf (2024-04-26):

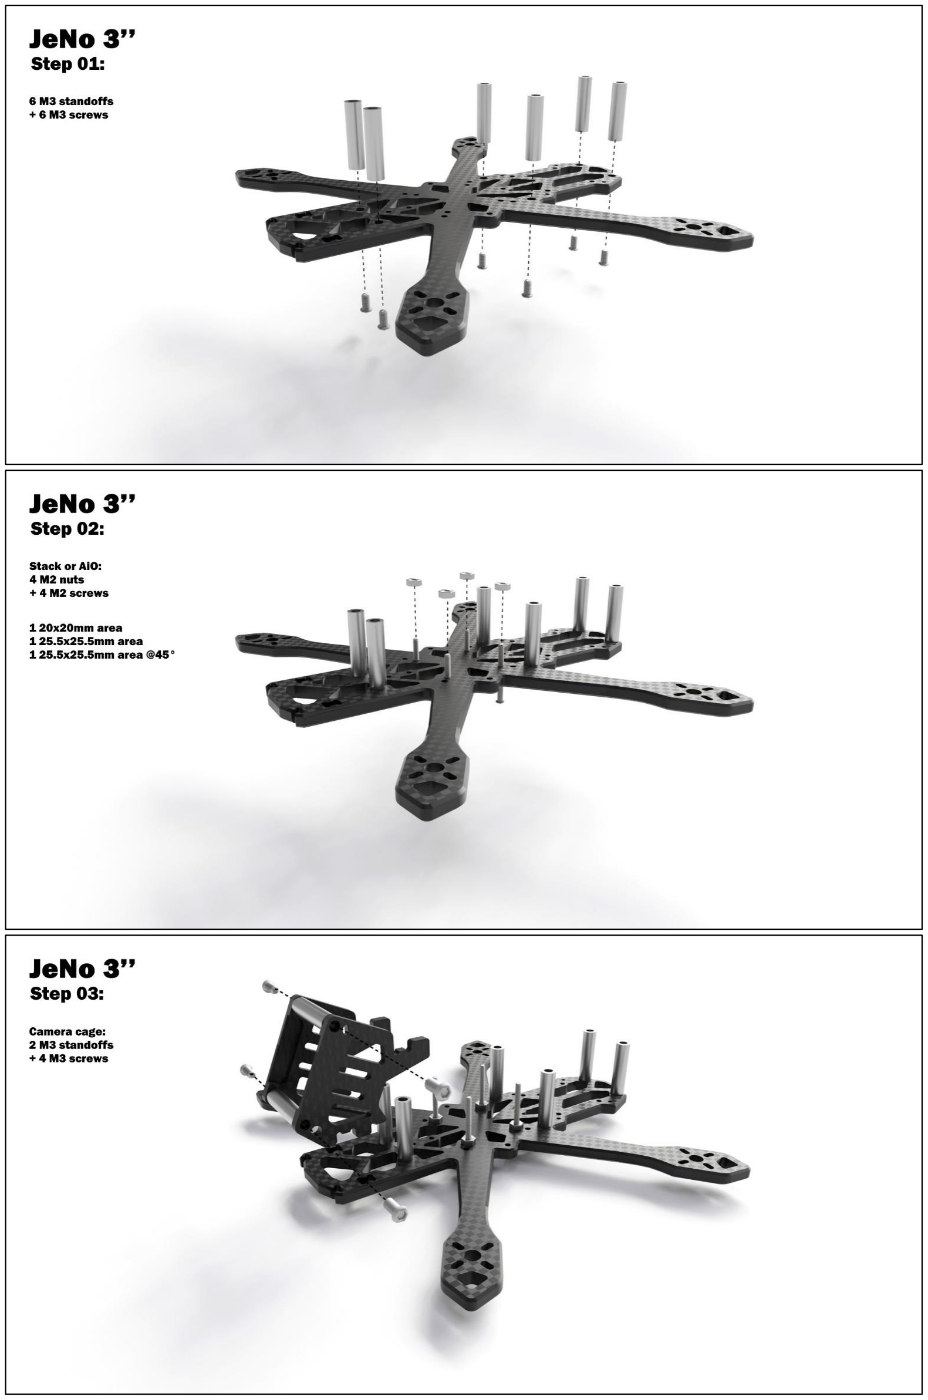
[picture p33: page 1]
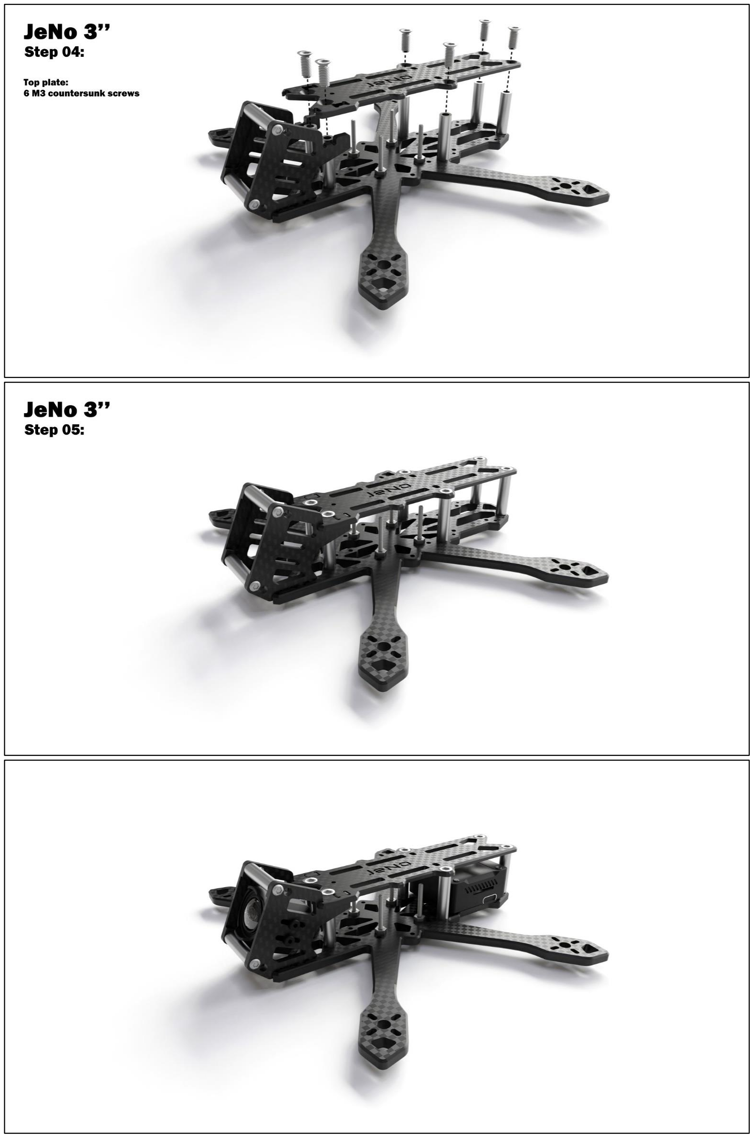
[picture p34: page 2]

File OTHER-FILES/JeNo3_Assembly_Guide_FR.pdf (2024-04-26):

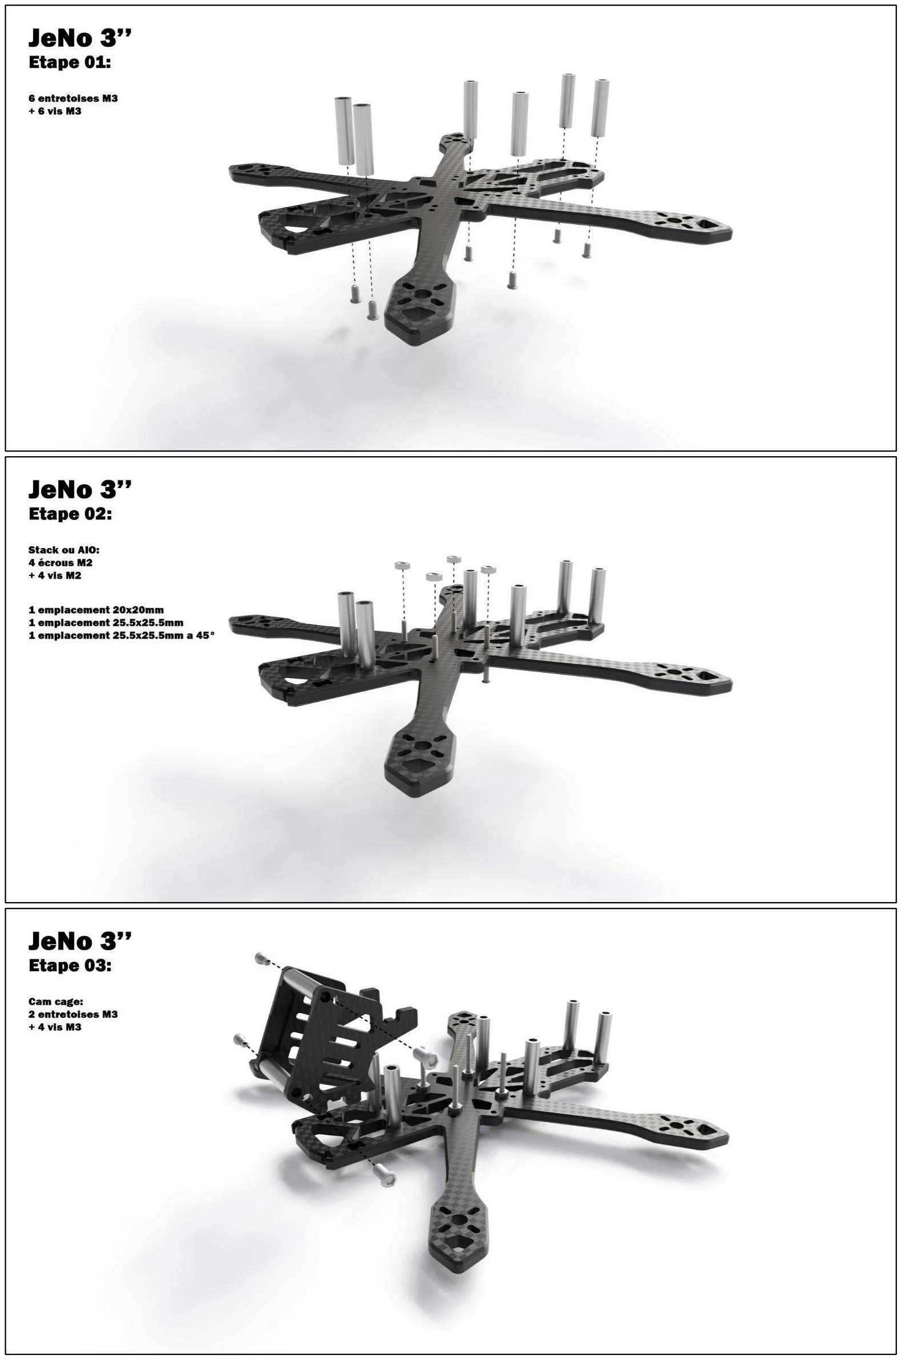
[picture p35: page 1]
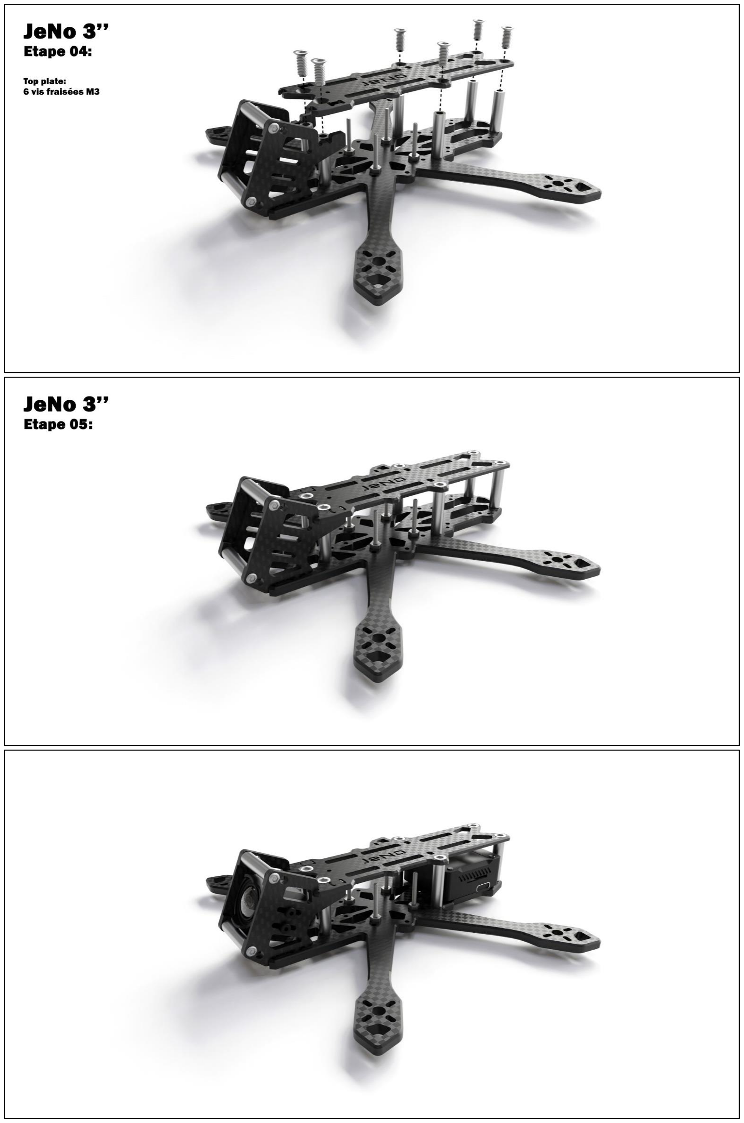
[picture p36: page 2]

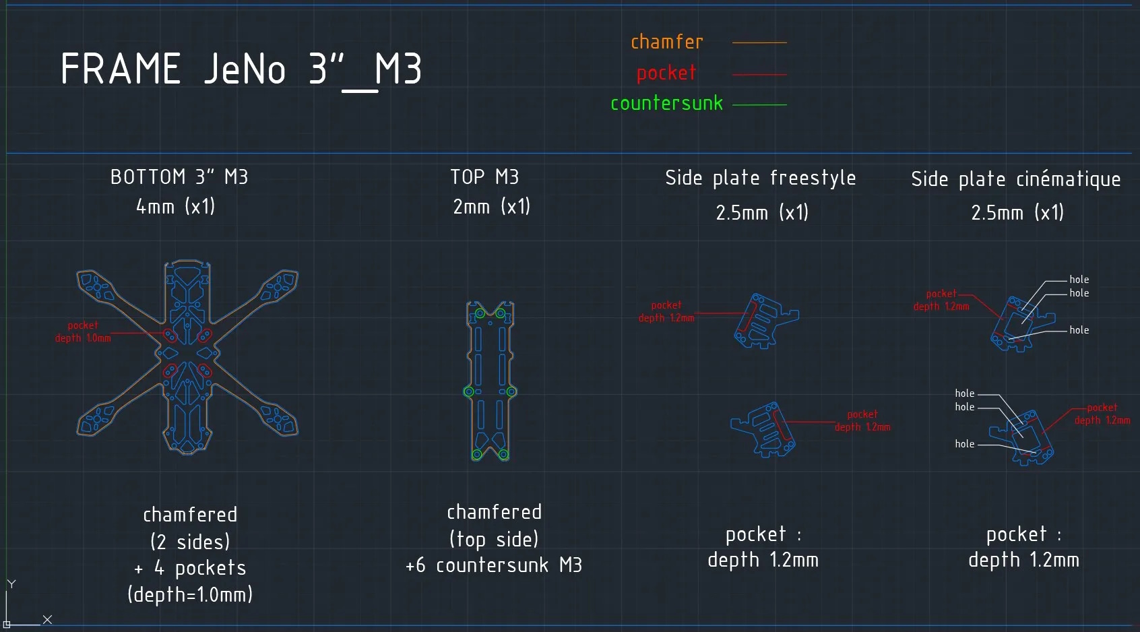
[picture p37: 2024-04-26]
images/JeNo3_BluePrint.jpg

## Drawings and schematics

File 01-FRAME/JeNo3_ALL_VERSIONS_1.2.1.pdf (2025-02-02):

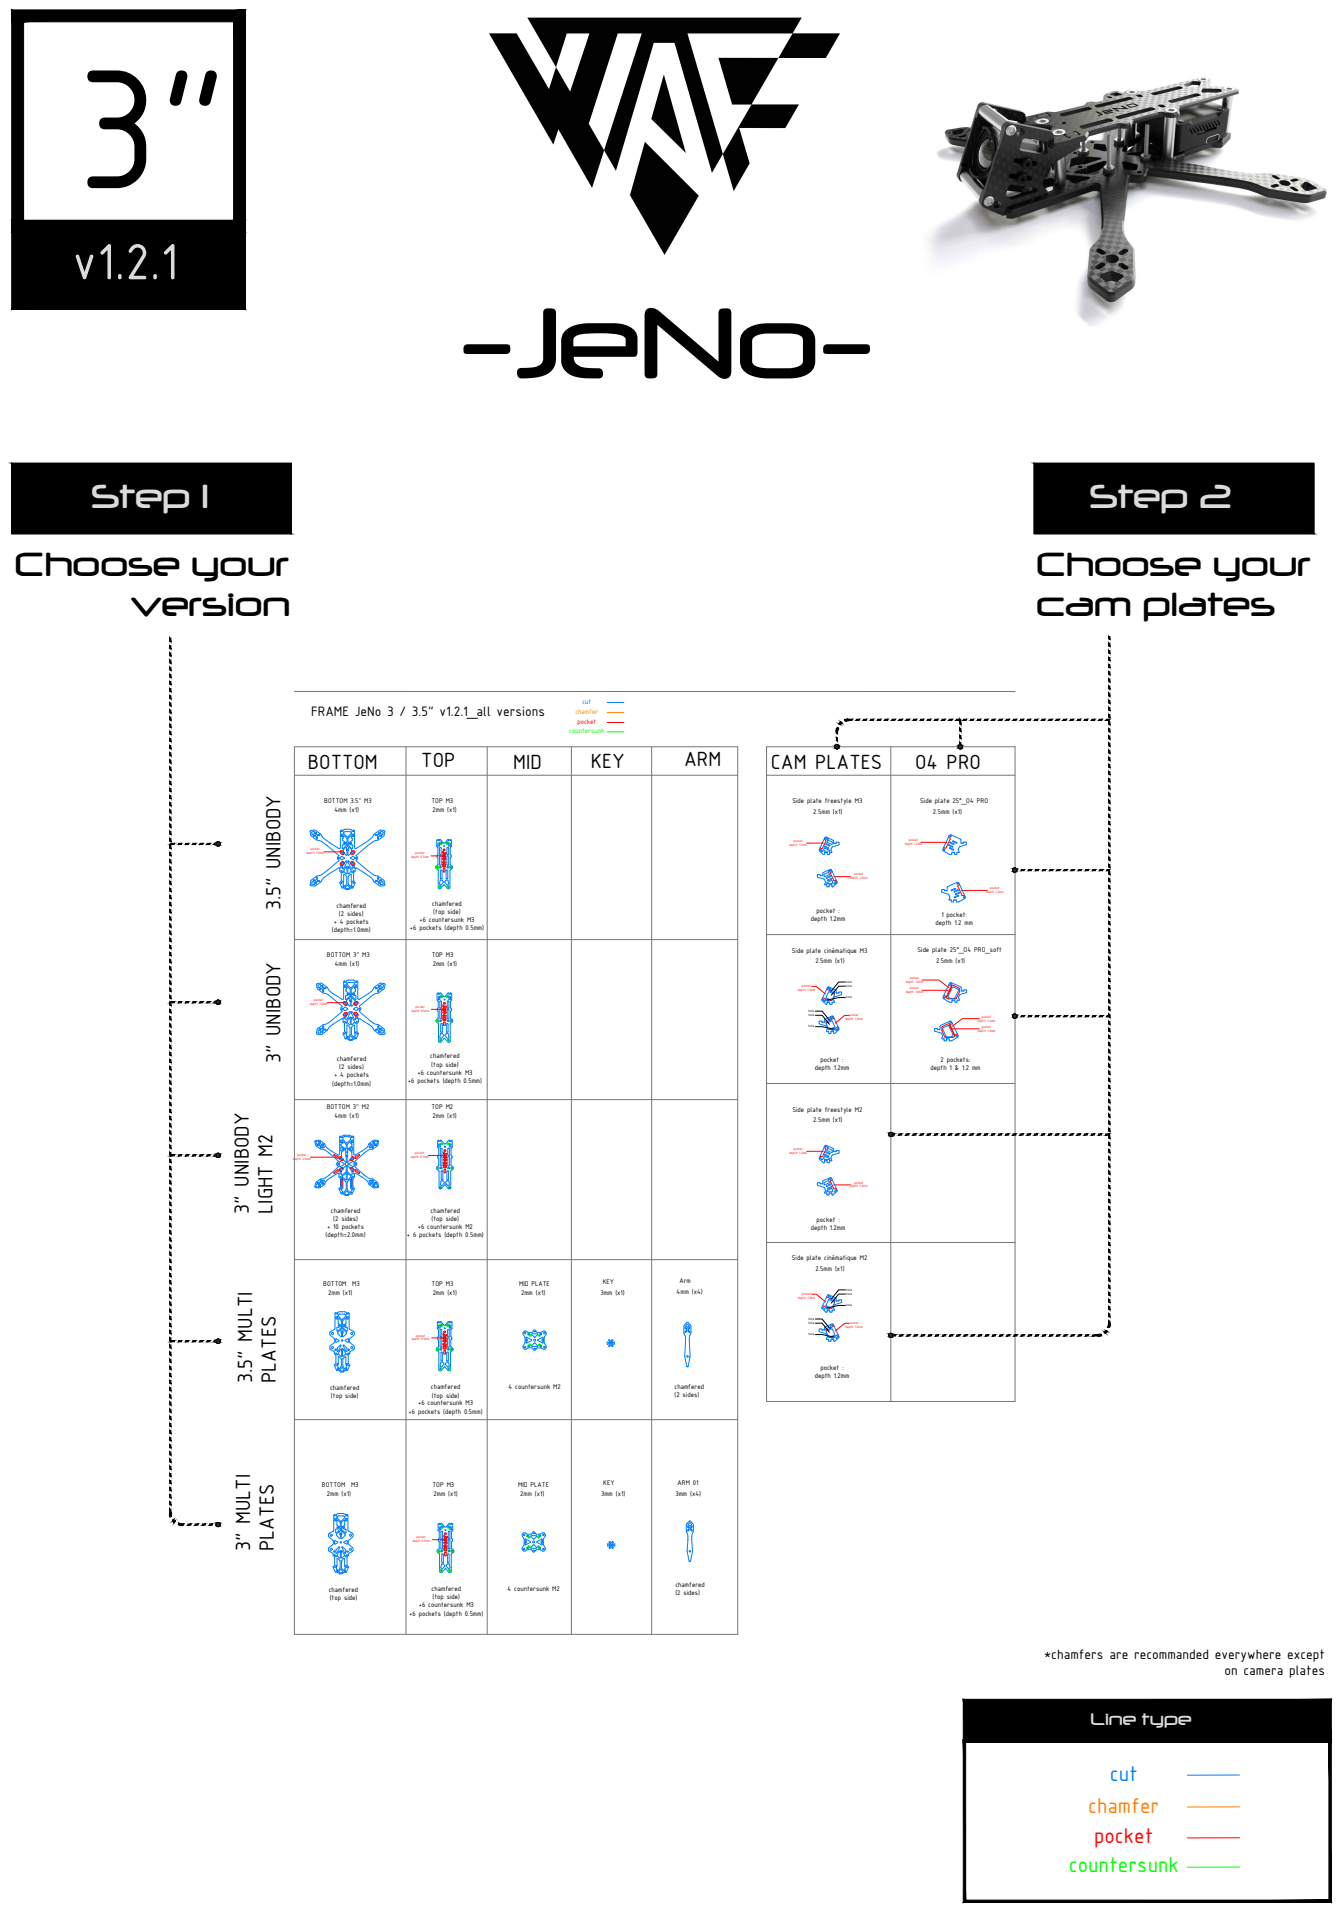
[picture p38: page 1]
BOTTOM 3.5" M3; pocket : depth 1.2mm; (2 sides) + 4 pockets; TOP M3; pocket depth 1.2mm; pocket depth 1.0mm; chamfered; (top side) +6 countersunk M3 +6 pockets (depth 0.5mm); pocket depth 0.5mm BOTTOM; TOP; MID; KEY; ARM; CAM PLATES 3.5" UNIBODY; pocket depth 2.0mm; BOTTOM M3; (top side); (2 sides); ARM 01; MID PLATE; 4 countersunk M2; pocket depth 0.5mm; 1 pocket: depth 1.2 mm; O4 PRO; Choose your; Choose your cam plates; Step 1 Step 2; Line type

FRAME JeNo 3 / 3.5" v1.2.1_all versions

Side plate freestyle M3

Side plate 25°_O4 PRO

Side plate cinématique M3 hole 2.5mm (x1) hole hole pocket depth 1.2mm hole hole pocket depth 1.2mm hole pocket : depth 1.2mm | Side plate 25°_O4 PRO_soft pocket depth 1.0mm 2.5mm (x1) pocket depth 1.2mm pocket depth 1.2mm pocket depth 1.0mm 2 pockets: depth 1 & 1.2 mm

BOTTOM 3" M3 4mm (x1) (2 sides) + 4 pockets (depth=1.0mm) | TOP M3 +6 pockets (depth 0.5mm) 3" UNIBODY 2mm (x1) pocket depth 0.5mm chamfered (top side) +6 countersunk M3

BOTTOM 3" M2 4mm (x1) (2 sides) + 10 pockets (depth=2.0mm) | | TOP M2 pocket depth 0.5mm 3" UNIBODY LIGHT M2 2mm (x1) chamfered (top side) +6 countersunk M2 + 6 pockets (depth 0.5mm)

Side plate freestyle M2 2.5mm (x1) pocket depth 1.2mm pocket depth 1.2mm pocket : depth 1.2mm

Side plate cinématique M2 hole 2.5mm (x1) hole pocket depth 1.2mm hole hole hole pocket depth 1.2mm hole pocket : depth 1.2mm

BOTTOM M3 2mm (x1) | | TOP M3 pocket depth 0.5mm 2mm (x1) chamfered (top side) +6 countersunk M3 +6 pockets (depth 0.5mm) | MID PLATE 2mm (x1) 4 countersunk M2 | KEY 3mm (x1) | Arm 3.5" MULTI PLATES 3" MULTI PLATES 4mm (x4) chamfered (2 sides)

*chamfers are recommanded everywhere except

on camera plates

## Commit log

2024-04-26 Load repo files from Printables
    [JeNo3_ArmProtect_Bando.stl, JeNo3_BackBumper_Flat.stl, JeNo3_FrontBumper.stl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]
2025-02-02 Version 1.2.1 : O4 Pro compatibility
    [JeNo3_1.1_FrontBumper.stl, JeNo3_1.1_NanoCamera.stl, JeNo3_1.1_SoftMount_Left.stl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]
2025-02-09 1.2.1 update
    [JeNo3_ALL_VERSIONS_1.2.1.step, JeNo3_ALL_VERSIONS_1.2.1.stl, JeNo3_ALL_VERSIONS_1.2.step]
2025-02-16 TPU for softmounted cam plates O4 and O3
    [JeNo3_Softmount_O4_O3_Left.stl, JeNo3_Softmount_O4_O3_Right.stl]
2025-05-23 TPU update
    [JeNo3_Antenna_O4_Pro_Full.stl, JeNo3_CapHat.stl, JeNo3_FrontBumper_O4_Pro.stl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]
2025-09-02 Apply line ending normalization for DXF
    [JeNo3_ALL_VERSIONS_1.1.dxf, JeNo3_ALL_VERSIONS_1.2.1.dxf]

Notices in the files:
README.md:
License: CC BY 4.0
